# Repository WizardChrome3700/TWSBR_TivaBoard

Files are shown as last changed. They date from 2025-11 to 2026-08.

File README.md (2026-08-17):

### Project Report:-
[Group I ME6102 Presentation .pdf](https://github.com/WizardChrome3700/TWSBR_TivaBoard/blob/master/Group%20I%20ME6102%20Presentation%20.pdf) is the project presentation. There was no report but we were required to submit [build instructions](https://github.com/WizardChrome3700/TWSBR_TivaBoard/blob/master/Build_instructions.pdf).

### Pinout of Tiva C Launchpad
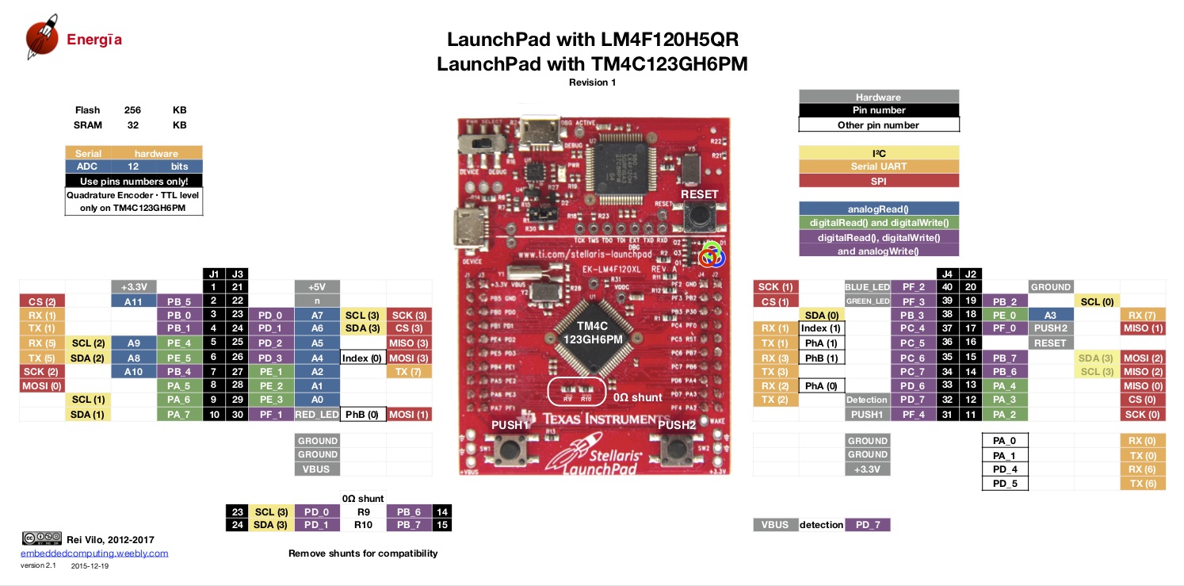
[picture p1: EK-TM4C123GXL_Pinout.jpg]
TIVA TM4C123GH6PM


### Connection Summary
|Component|Pin|Connected To |Signal |Description |
|---|---|---|---|---|
|JST6A |1  |TB1 pin 1 |motor1_M1 |Motor 1 terminal A |
|JST6A |2  |Tiva +3.3 V |3V3 |Encoder supply |
|JST6A |3  |Tiva PC5 |Encoder1_PHA |Encoder Channel A |
|JST6A |4  |Tiva PC6 |Encoder1_PHB |Encoder Channel B |
|JST6A |5  |Tiva GND |GND |Common ground |
|JST6A |6  |TB1 pin 2 |motor1_M2 |Motor 1 terminal B |
|JST3A |1  |Tiva PB4 |IN1_motor_driver |Motor 1 input 1 |
|JST3A |2  |Tiva PB5 |IN2_motor_driver |Motor 1 input 2 |
|JST3A |3  |Tiva PE4 |ENA_motor_driver |Motor 1 enable signal |
|JST6B |1  |TB2 pin 1 |motor2_M2 |Motor 2 terminal A |
|JST6B |2  |Tiva +3.3 V |3V3 |Encoder supply |
|JST6B |3  |Tiva PF0 |Encoder2_PHA |Encoder Channel A |
|JST6B |4  |Tiva PD7 |Encoder2_PHB |Encoder Channel B |
|JST6B |5  |Tiva GND |GND |Common ground |
|JST6B |6  |TB2 pin 2 |motor2_M1 |Motor 2 terminal B |
|JST3B |1  |Tiva PB6 |IN3_motor_driver |Motor 2 input 1 |
|JST3B |2  |Tiva PB7 |IN4_motor_driver |Motor 2 input 2 |
|JST3B |3  |Tiva PD6 |ENB_motor_driver |Motor 2 enable signal |
|TB1 |1  |JST6A pin 1 |motor1_M1 |Motor 1 terminal A |
|TB1 |2  |JST6A pin 6 |motor1_M2 |Motor 1 terminal B |
|TB2 |1  |JST6B pin 1 |motor2_M2 |Motor 2 terminal A |
|TB2 |2  |JST6B pin 6 |motor2_M1 |Motor 2 terminal B |
|R1 |-  |3.3V ↔ Tiva PB2|4.7kΩ |Pull-up or signal conditioning |
|R2 |-  |3.3V ↔ Tiva PB3|4.7kΩ |Pull-up or signal conditioning |
|ESP01 |7  |Tiva PB1 |ESP_RX |UART Recieve(ESP) to UART Transmit(Tiva)|
|ESP01 |2  |Tiva PB0 |ESP_TX |UART Transmit(ESP) to UART Recieve(Tiva)|
|ESP01 |8  |Tiva +3.3 V |3V3 |Power ESP01 |
|ESP01 |1  |Tiva GND |GND |Common ground |
|ESP01 |4  |Tiva +3.3 V |ESP_CH_EN |Enable ESP01 to communicate |
|MPU9250  |1  |Tiva +3.3 V |MPU9520_VCC |Power MPU9250 |
|MPU9250  |2  |Tiva GND |GND |Common ground |
|MPU9250  |3  |Tiva PB2 |MPU9520_SCL |Serial clock of I2C of MPU9250 |
|MPU9250  |4  |Tiva PB3 |MPU9520_SDA |Serial data of I2C of MPU9250 |
|RLS08 |A1 |Tiva PD0 |Line follower IR1|ADC source of IR1 of Line follower |
|RLS08 |A2 |Tiva PD1 |Line follower IR1|ADC source of IR1 of Line follower |
|RLS08 |A3 |Tiva PD2 |Line follower IR1|ADC source of IR1 of Line follower |
|RLS08 |A4 |Tiva PD3 |Line follower IR1|ADC source of IR1 of Line follower |
|RLS08 |A5 |Tiva PE1 |Line follower IR1|ADC source of IR1 of Line follower |
|RLS08 |A6 |Tiva PE2 |Line follower IR1|ADC source of IR1 of Line follower |
|RLS08 |A7 |Tiva PE3 |Line follower IR1|ADC source of IR1 of Line follower |
|RLS08 |A8 |Tiva PE0 |Line follower IR1|ADC source of IR1 of Line follower |

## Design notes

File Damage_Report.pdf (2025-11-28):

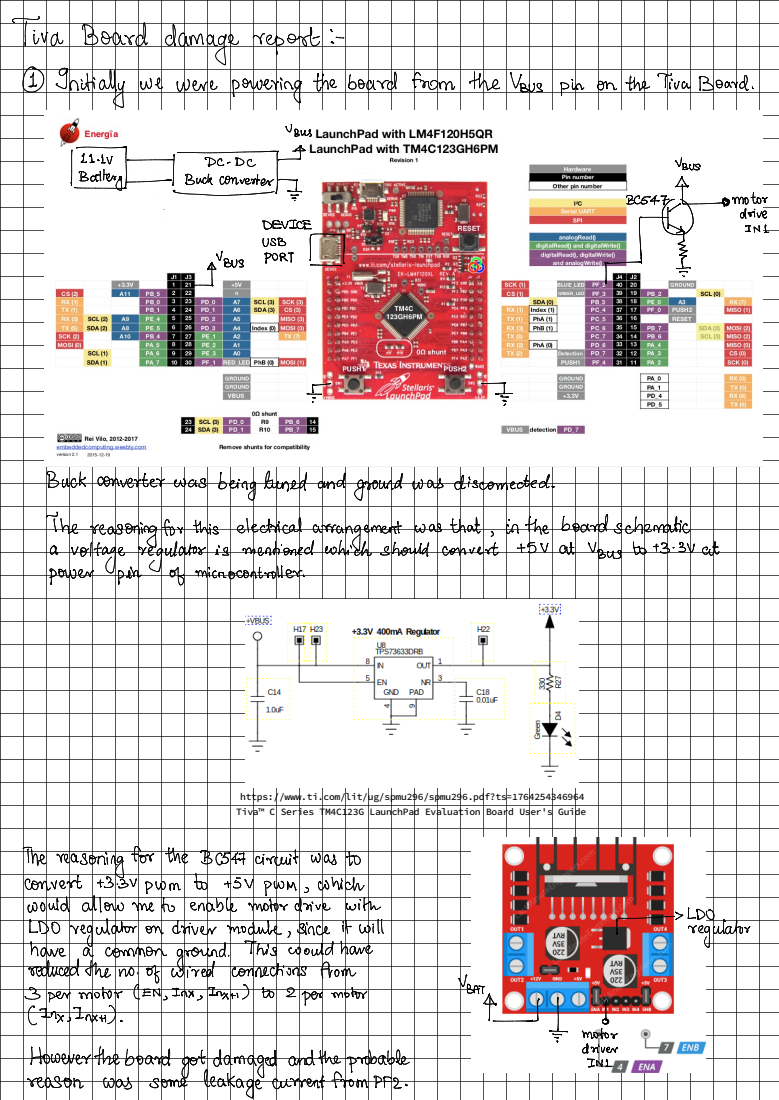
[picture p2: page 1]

https://www.ti.com/lit/ug/spmu296/spmu296.pdf?ts=1764254346964
Tiva™ C Series TM4C123G LaunchPad Evaluation Board User's Guide

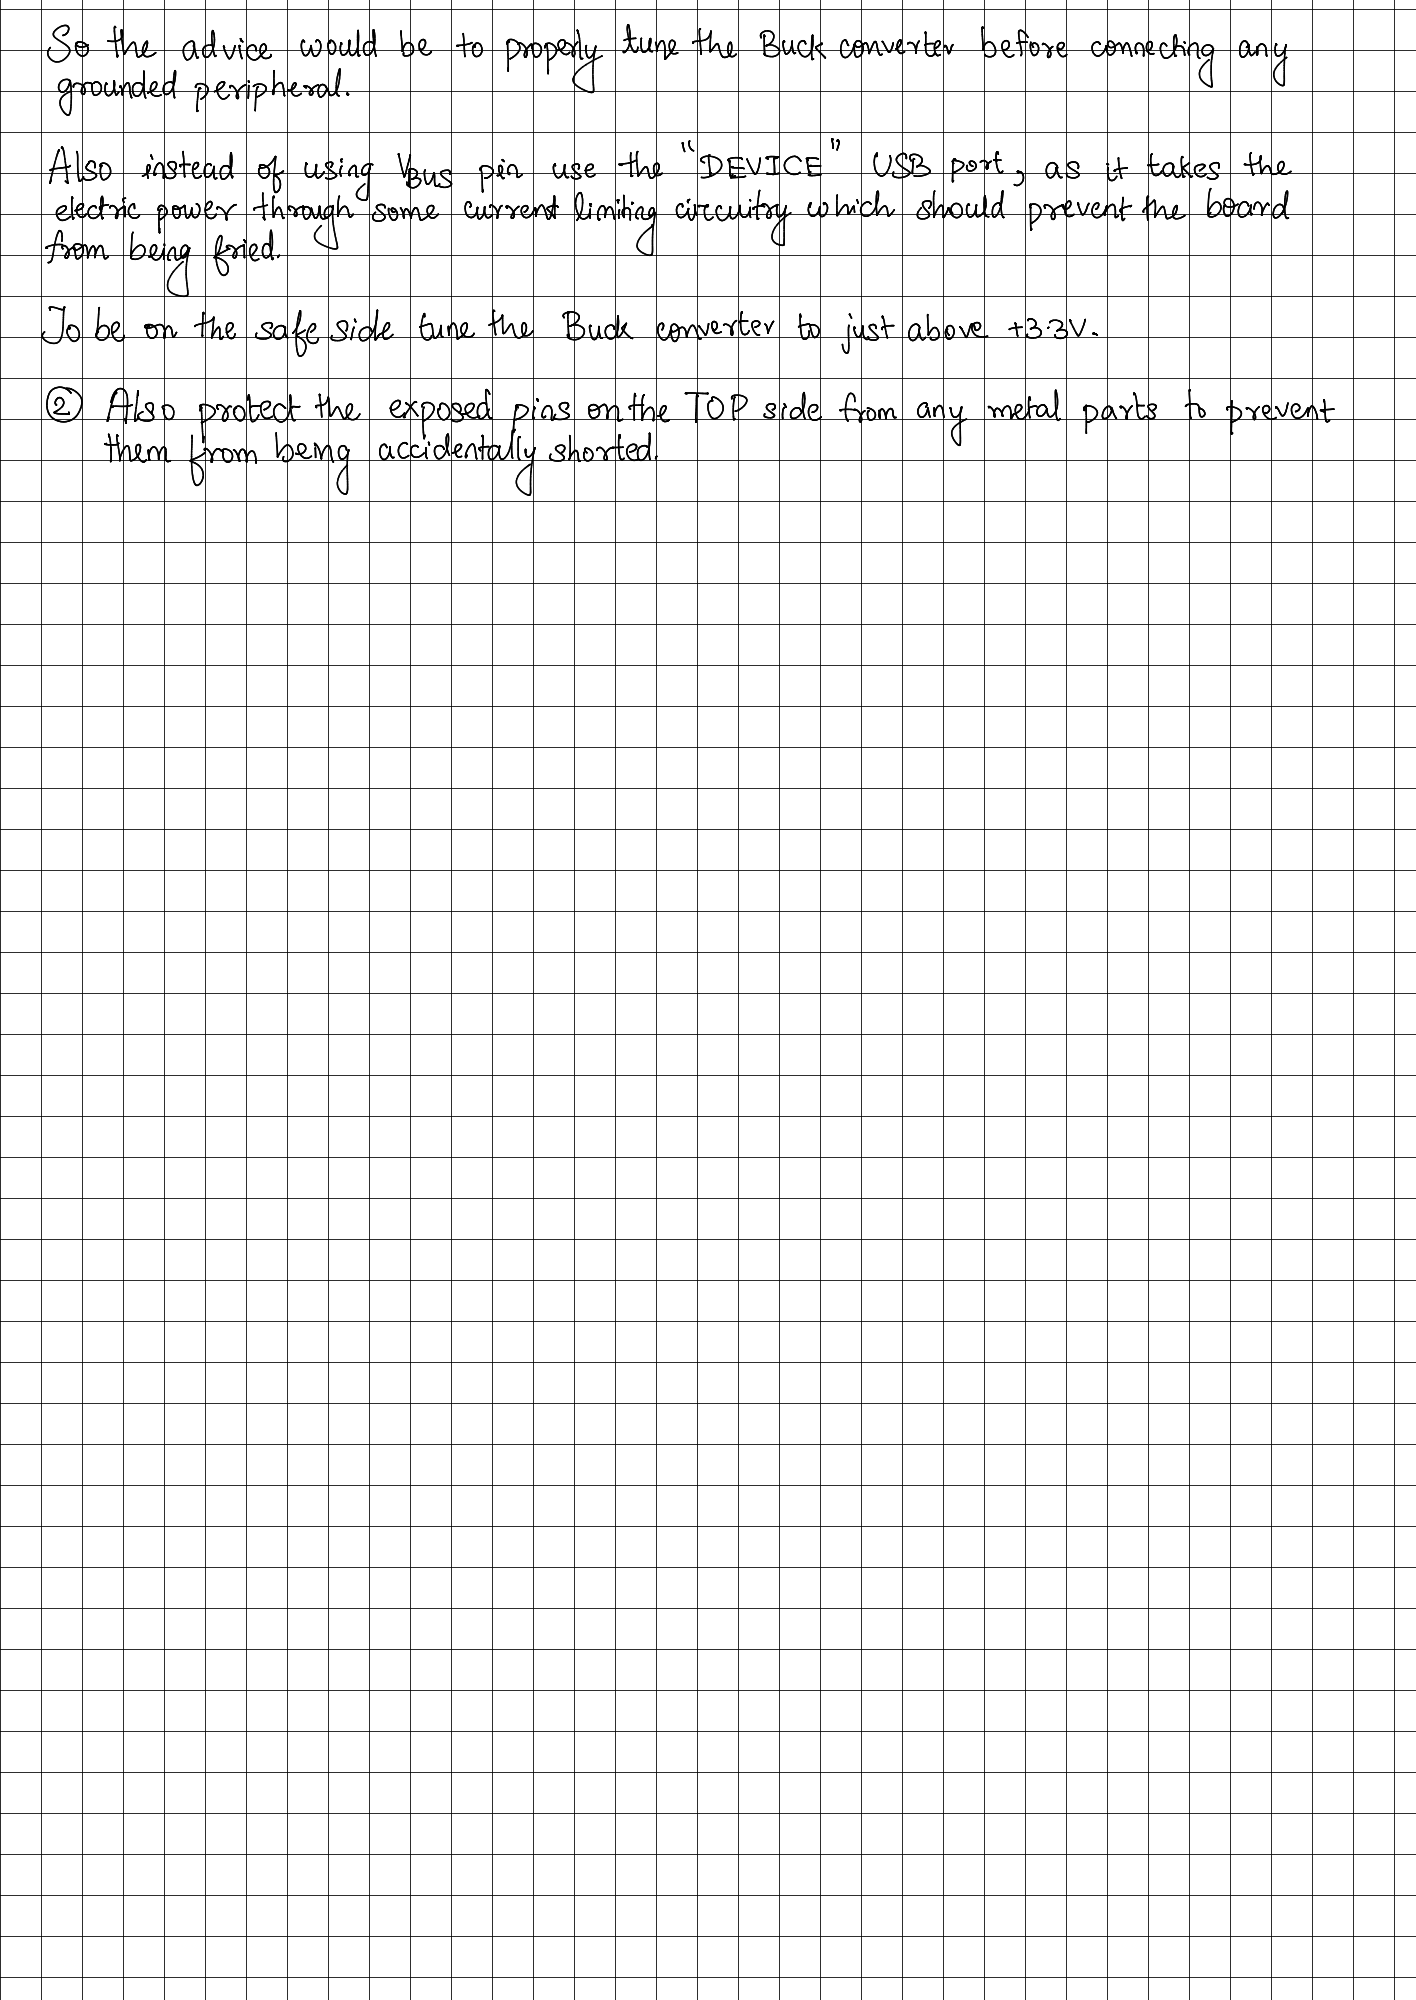
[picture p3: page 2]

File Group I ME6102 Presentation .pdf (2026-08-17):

# Design and Development of Self-Balancing Mobile Robot

Presented by- Group 1

Under the Guidance of

## (Prof. Prasanna S Gandhi)

# ME 6102- Project Stage IV

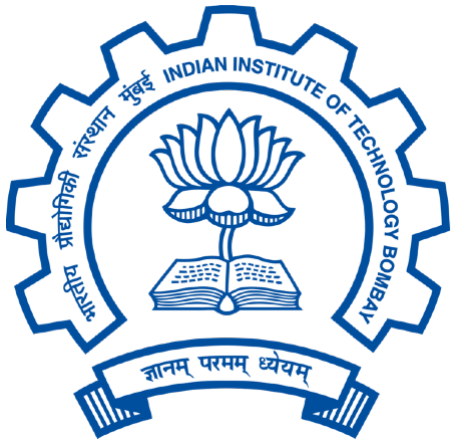
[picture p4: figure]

Indian Institute of Technology, Bombay

November 2025

## Department of Mechanical Engineering

Akshat Panda | Nishad PS | Sajal Thomas

# OUTLINE

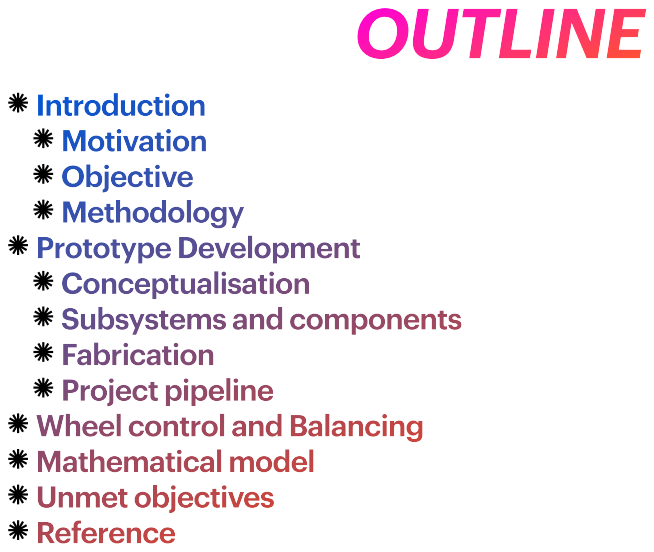
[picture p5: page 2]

Introduction
Motivation
Objective
Methodology
Prototype Development
Conceptualisation
Subsystems and components
Fabrication
Project pipeline
Wheel control and Balancing
Mathematical model
Unmet objectives
Reference

# Motivation

# Objective

# Methodology

We used the Tiva C Series microcontroller as the main controller for all real-time operations.
The robot integrates IMU for tilt estimation and encoders for wheel speed feedback. The mechanical structure is made using laser-cut acrylic plates assembled with spacers. The electrical system (motor driver, buck converter, sensors) is neatly integrated with the chassis.
The firmware was developed in Code Composer Studio using TivaWare driver libraries.

Design and development of a robot with TIVA microcontroller capable of self balancing and line following capabilities

To study the real world application of inverted single pendulum system Demonstrates practical implementation of PID control, sensor fusion, and real-time embedded processing.

# System Layout

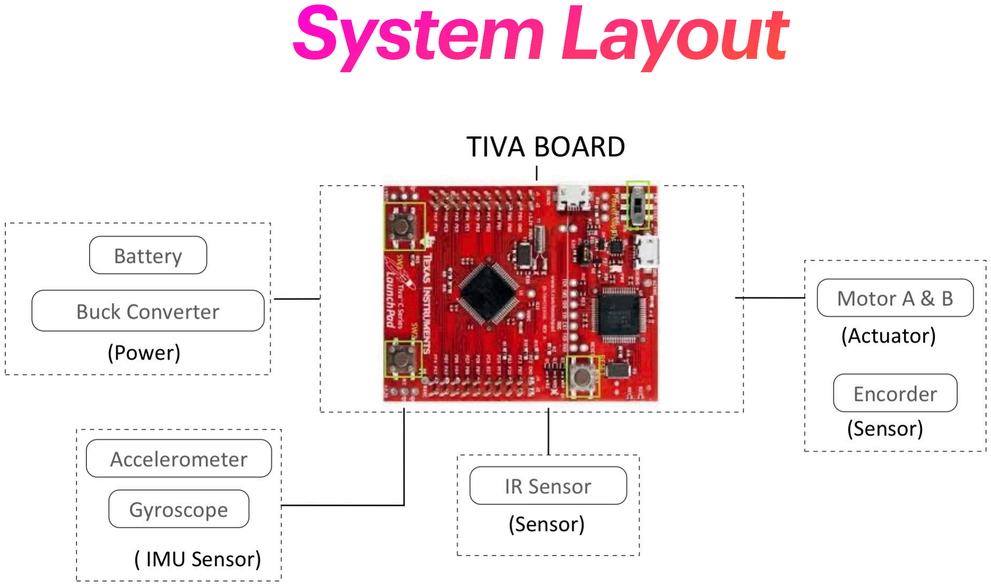
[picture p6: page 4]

# Conceptualisation

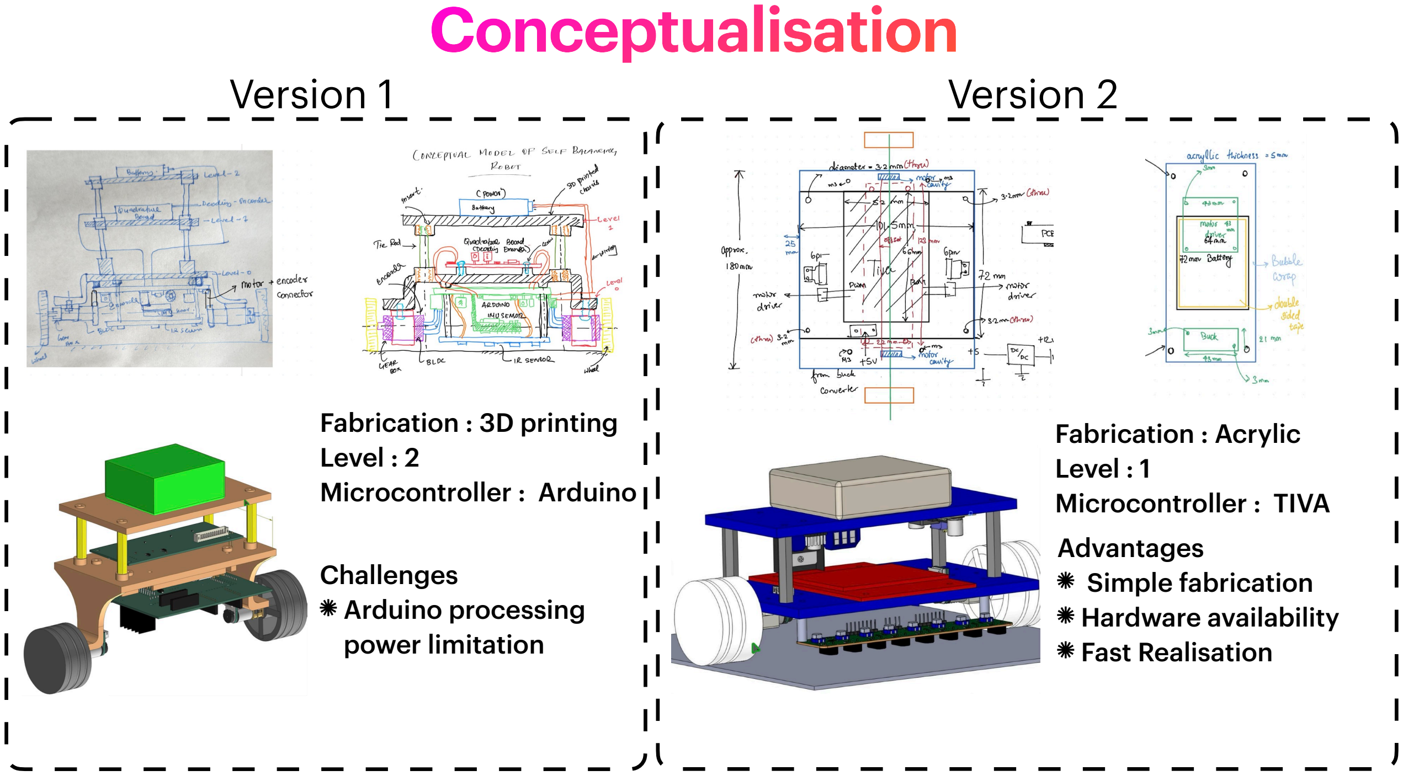
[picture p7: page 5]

Version 1 | Version 2

Fabrication : 3D printing
Level : 2
Microcontroller : Arduino

Challenges
Arduino processing
power limitation

Fabrication : Acrylic
Level : 1
Microcontroller : TIVA
Advantages
Simple fabrication
Hardware availability
Fast Realisation

# Specifications

### Microcontroller : TIVA C series Motor : GA12- N20 DC Motor (12V) Buck Converter - LM2596S Motor Drive - L298N Wheel - N20 Wheel 44mm dia Sensors - Encorder : Pro-range OE-28 - IMU - MPU 9250 - IR - RLS 08 Analog & Digital Line sensor array

# System Layout

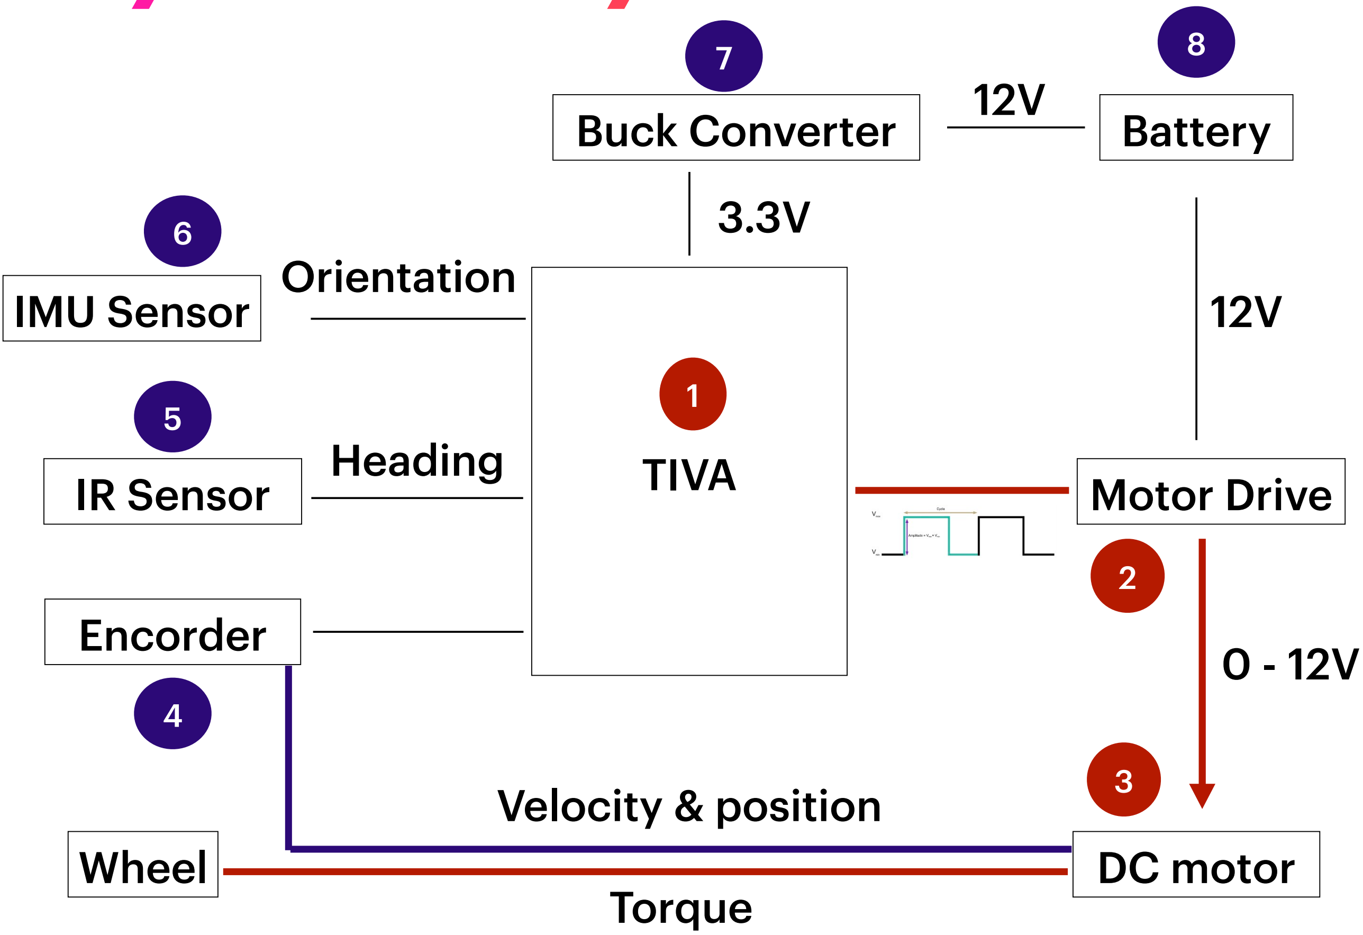
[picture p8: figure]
Wheel; DC motor; Motor Drive; Buck Converter; Battery; TIVA IR Sensor; IMU Sensor; Encorder; Velocity & position; Heading; Orientation; Torque
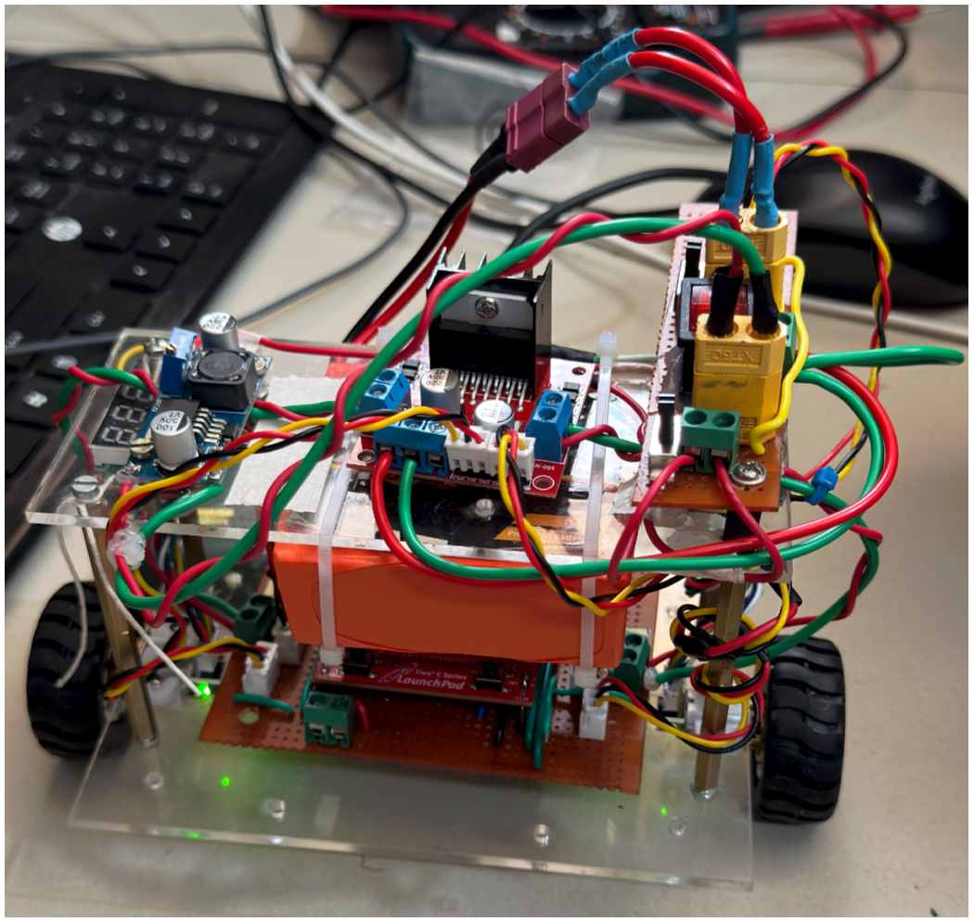
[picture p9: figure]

# Fabrications

## Mechanical integration

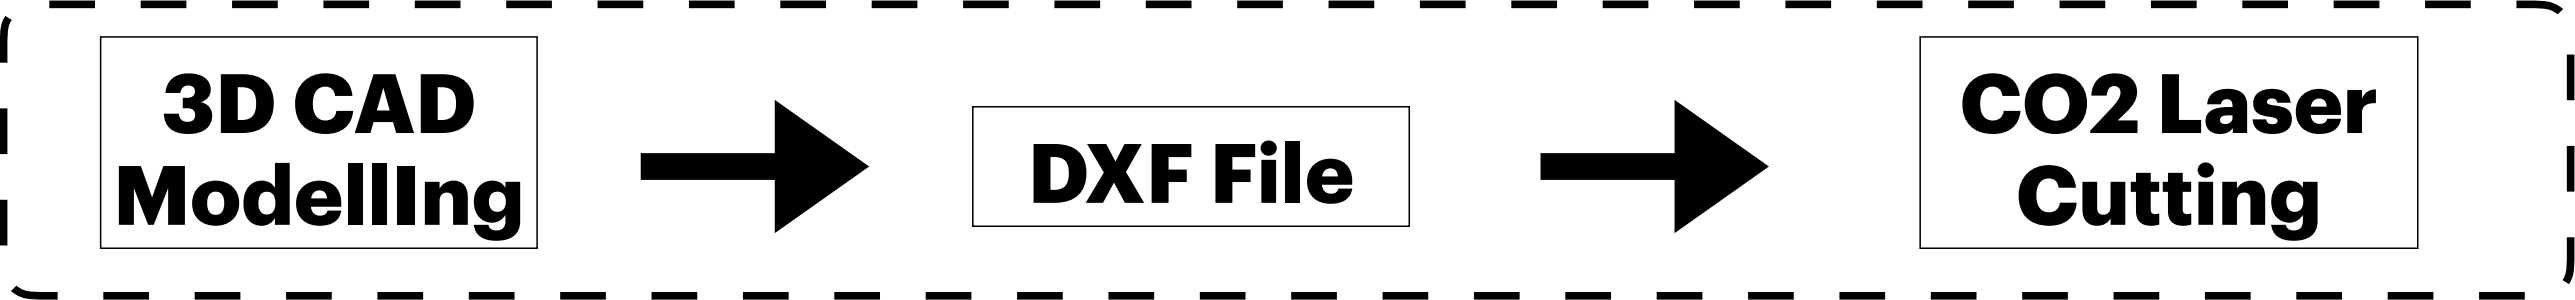
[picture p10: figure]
3D CAD; ModellIng; DXF File; CO2 Laser Cutting

## Electrical integration

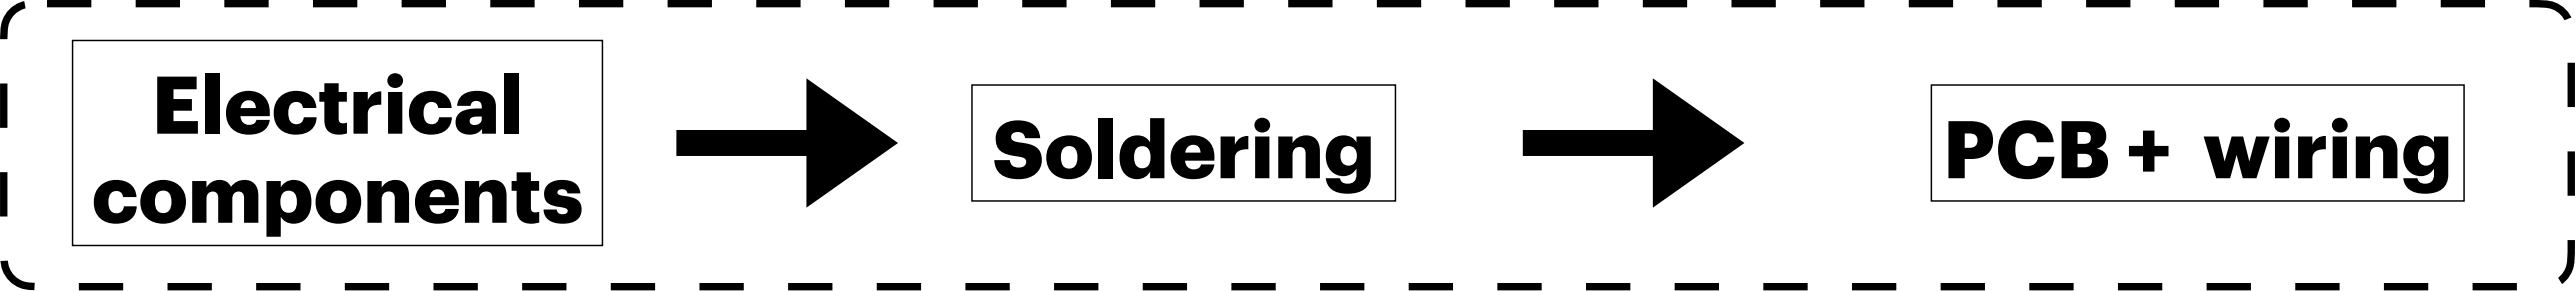
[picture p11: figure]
Electrical; components; Soldering; PCB + wiring
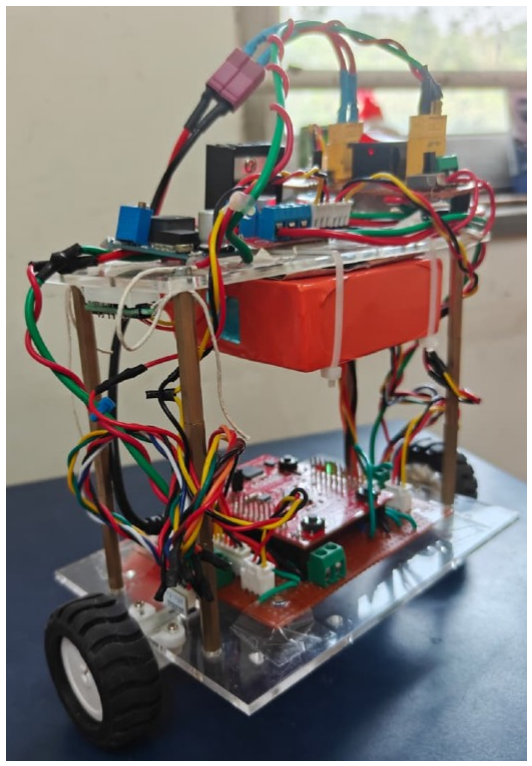
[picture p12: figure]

Laser cut acrylic

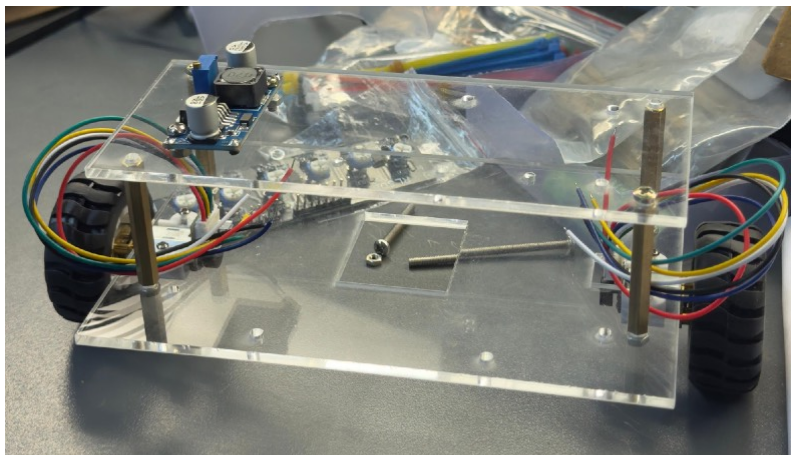
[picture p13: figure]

sheet | Assembly of both the
| levels

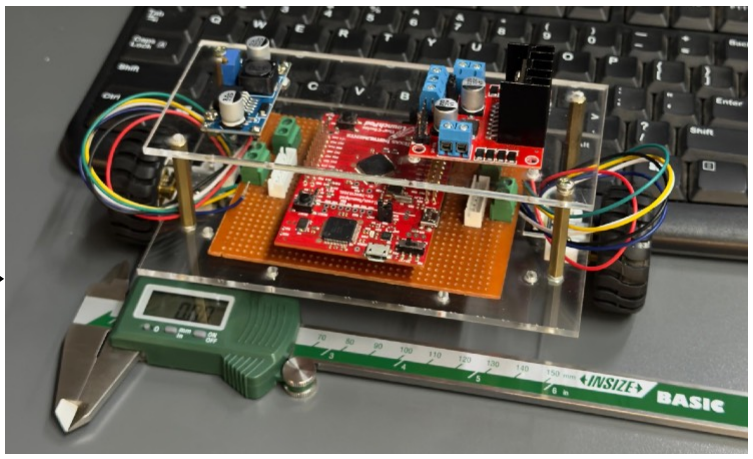
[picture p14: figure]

Assembly of TiVA
Microcontroller 3D CAD

# PROJECT PIPELINE

23 SEP | 23OCT | 05 Nov | 23 Nov

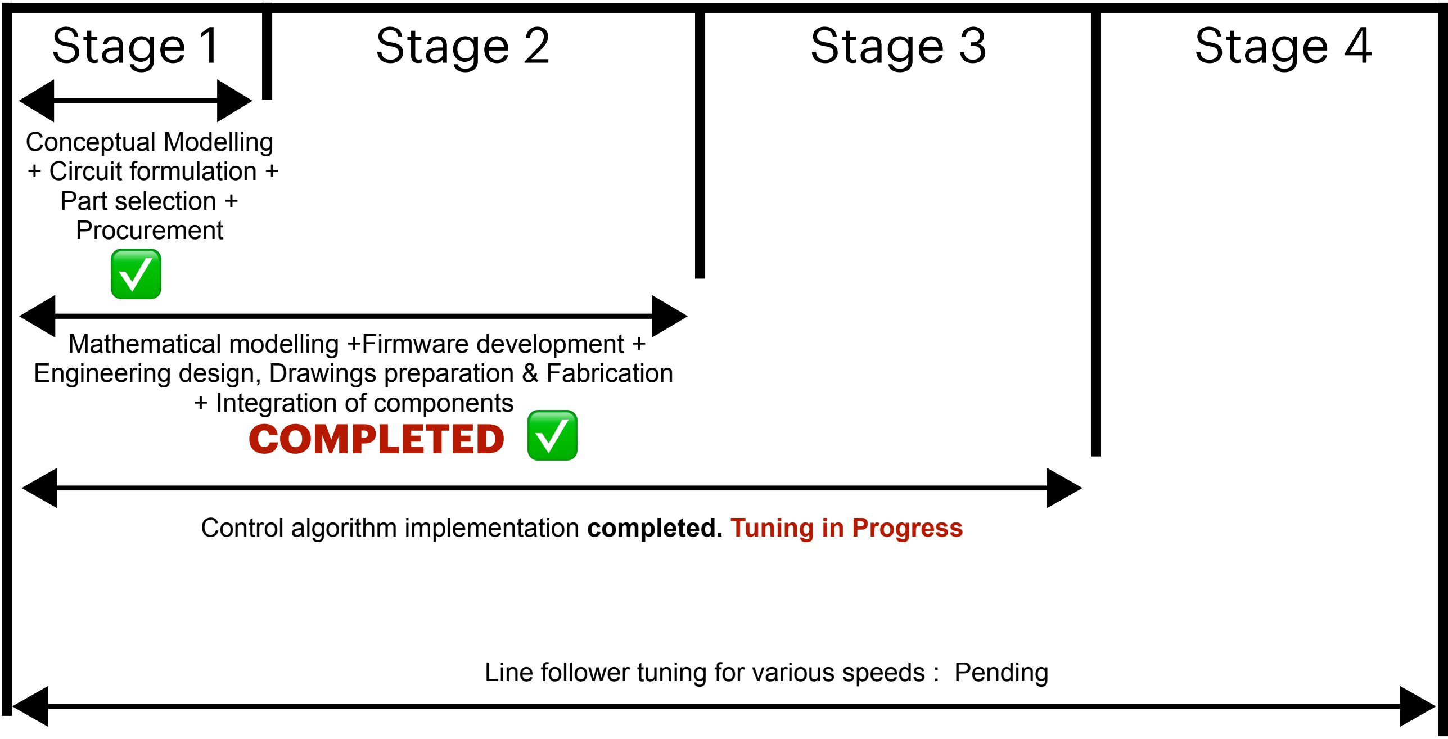
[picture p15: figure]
Stage 1; Stage 2; Stage 3; Stage 4; Conceptual Modelling + Circuit formulation + Part selection + Procurement; Mathematical modelling +Firmware development +; + Integration of components; COMPLETED

Engineering design, Drawings preparation & Fabrication

Control algorithm implementation completed. Tuning in Progress

Line follower tuning for various speeds : Pending

# Wheel Control

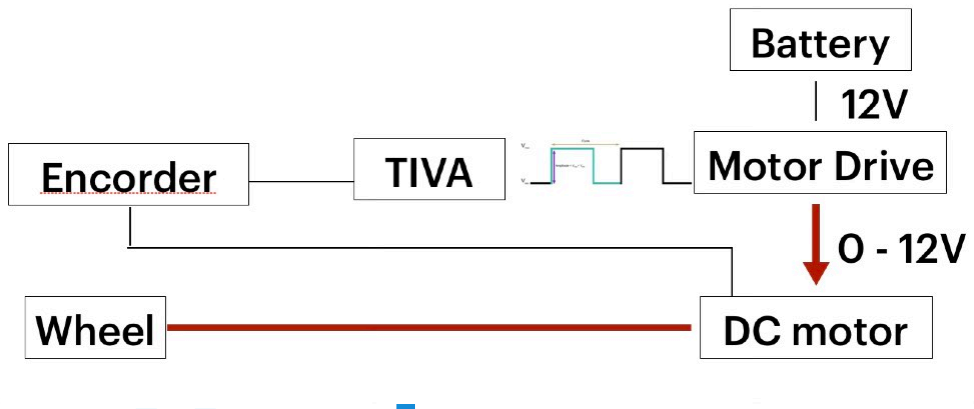
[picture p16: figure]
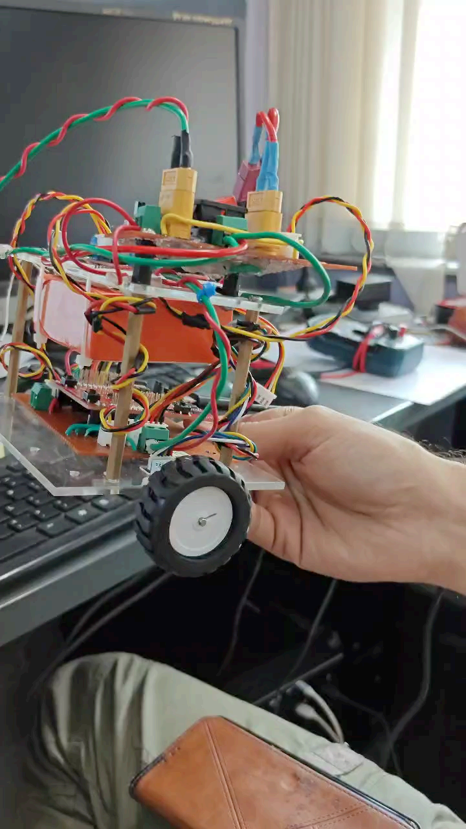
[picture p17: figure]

Micro Controller
TIVA C- Series
Battery
12V - Lithium ion battery
2500 mAH
Motor drive
L 298N
Voltage O/P: 0 - 12 V
Gear Ratio - 250:1
Motor
N20 DC motor

### 12 V, 0.6A

Torque = 2N-cm
Encorder
3 Pulse Per Revelution.

## Hardware

## Software

Software : Code Composer
Studio
Objective : Intuitive wheel control
Current Status : PWM
generation and Encorder
reading completed

Wheel control code (https://github.com/WizardChrome3700/TWSBR_TivaBoard/tree/master/TWSBR_Code_Base/TWSBR_Wheel)

# BALANCE CONTROL

## Hardware

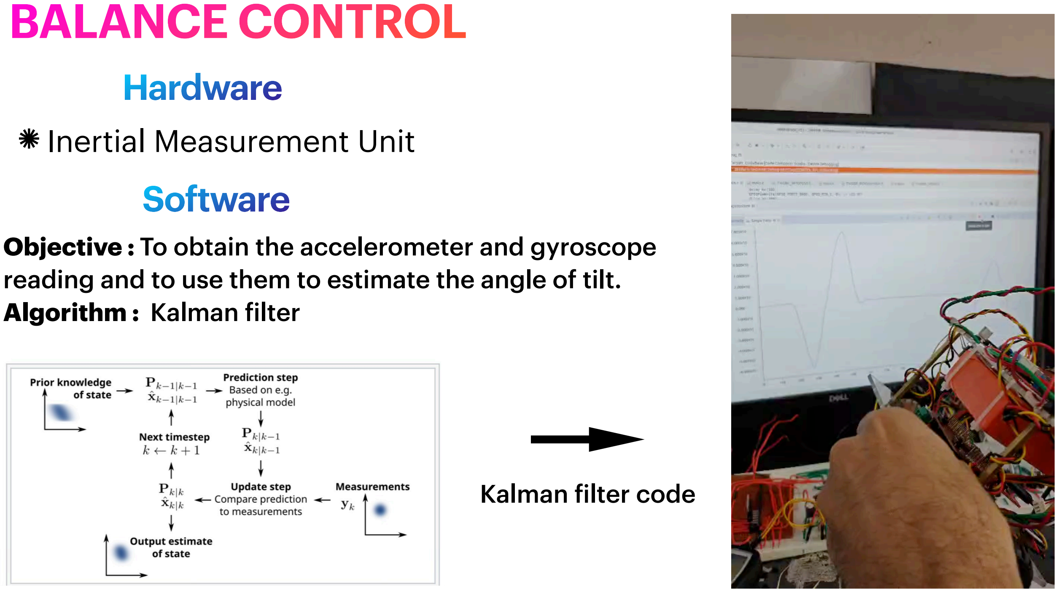
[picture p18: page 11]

### Inertial Measurement Unit

## Software

Objective : To obtain the accelerometer and gyroscope reading and to use them to estimate the angle of tilt. Algorithm : Kalman filter

Kalman filter code (https://github.com/WizardChrome3700/TWSBR_TivaBoard/tree/master/TWSBR_Code_Base/TWSBR_MPU9250)

# Mathematical modelling - Dynamics

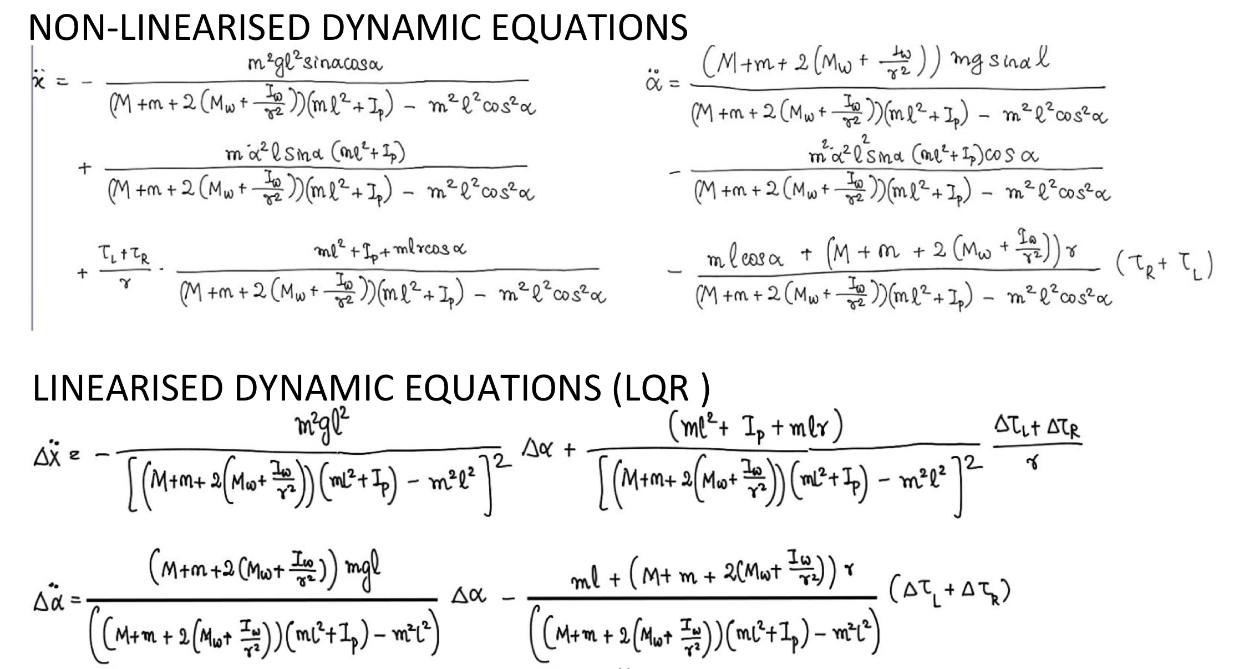
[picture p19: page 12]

# Mathematical modelling - Kalman Filter

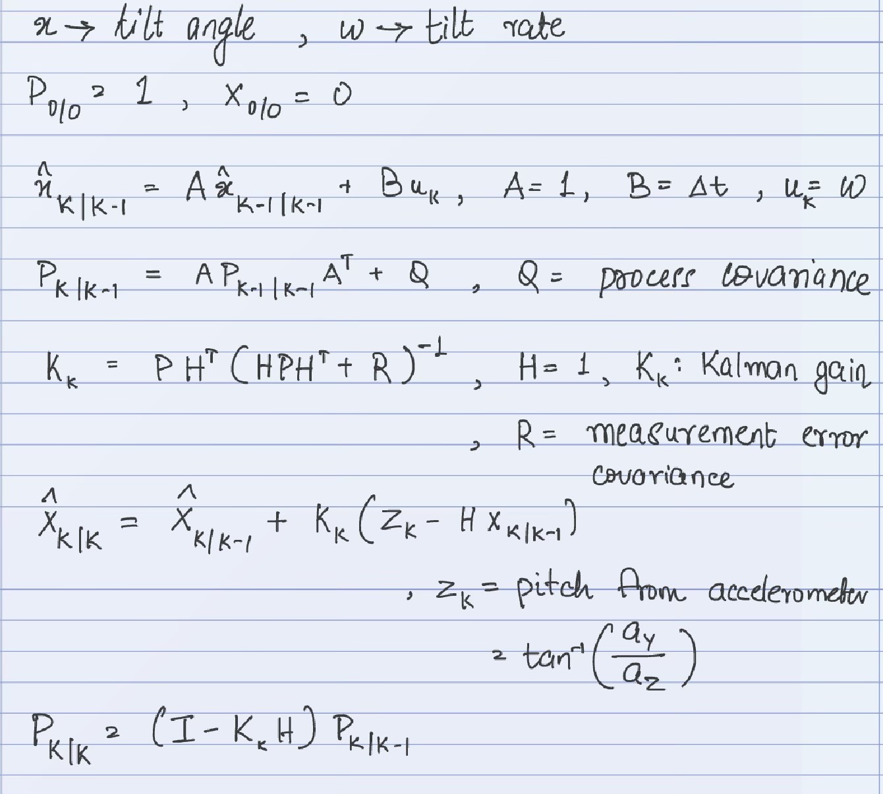
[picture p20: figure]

# Input and output of kalman filter

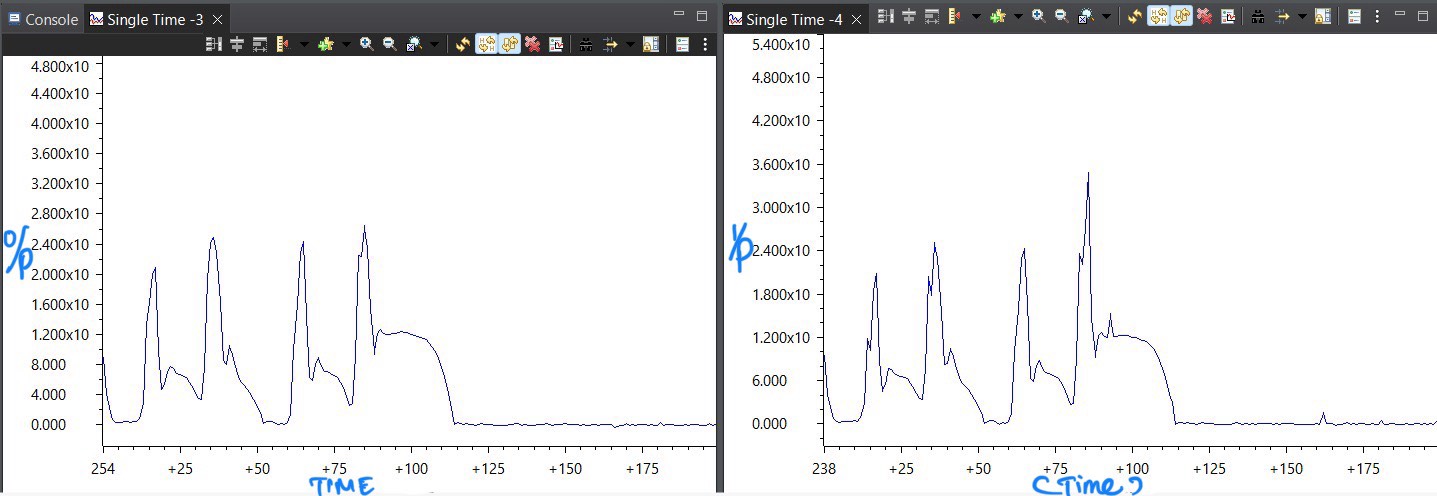
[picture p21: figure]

# UNMET OBJECTIVES

## Line-Following Feature Not Integrated Complete Stability Not Achieved

Despite integrating the IMU, motor driver, and Tiva C controller successfully, the robot did not reach complete stability because the PID control parameters (Kp, Ki, Kd) could not be fully optimized.
We performed multiple experiments by varying these gains, but the system continued to show oscillations and drift.
Achieving stable balance requires extensive tuning under different loading and surface conditions, which we could not complete within the available time. Therefore, additional testing and further PID refinement are needed to meet the stability objective

# Reason for not meeting the objectives

# Reference

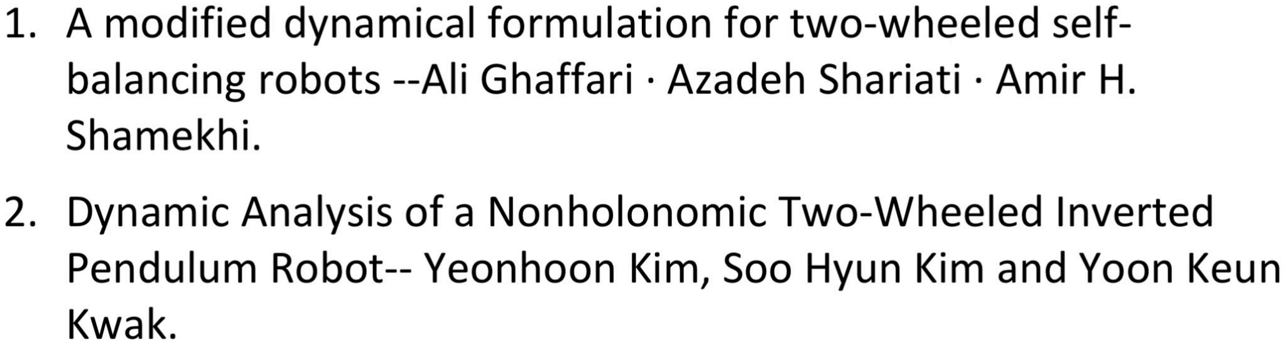
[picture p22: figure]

# Thank you

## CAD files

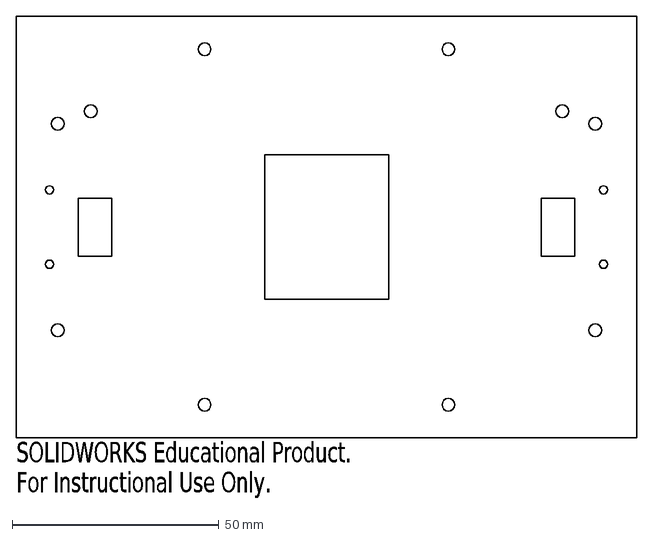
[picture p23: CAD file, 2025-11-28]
Mechanical Subsystem/Level0.DXF
SOLIDWORKS Educational Product.
For Instructional Use Only.

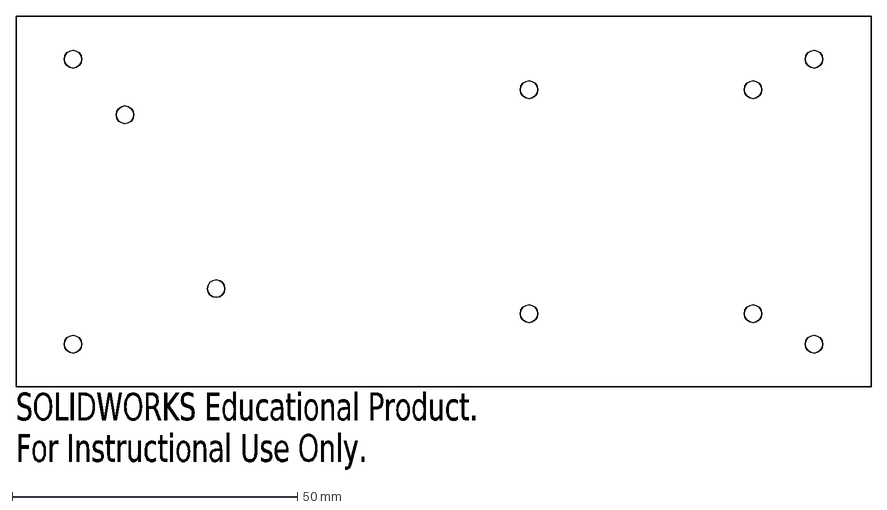
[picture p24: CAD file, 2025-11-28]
Mechanical Subsystem/Level1.DXF
SOLIDWORKS Educational Product.
For Instructional Use Only.

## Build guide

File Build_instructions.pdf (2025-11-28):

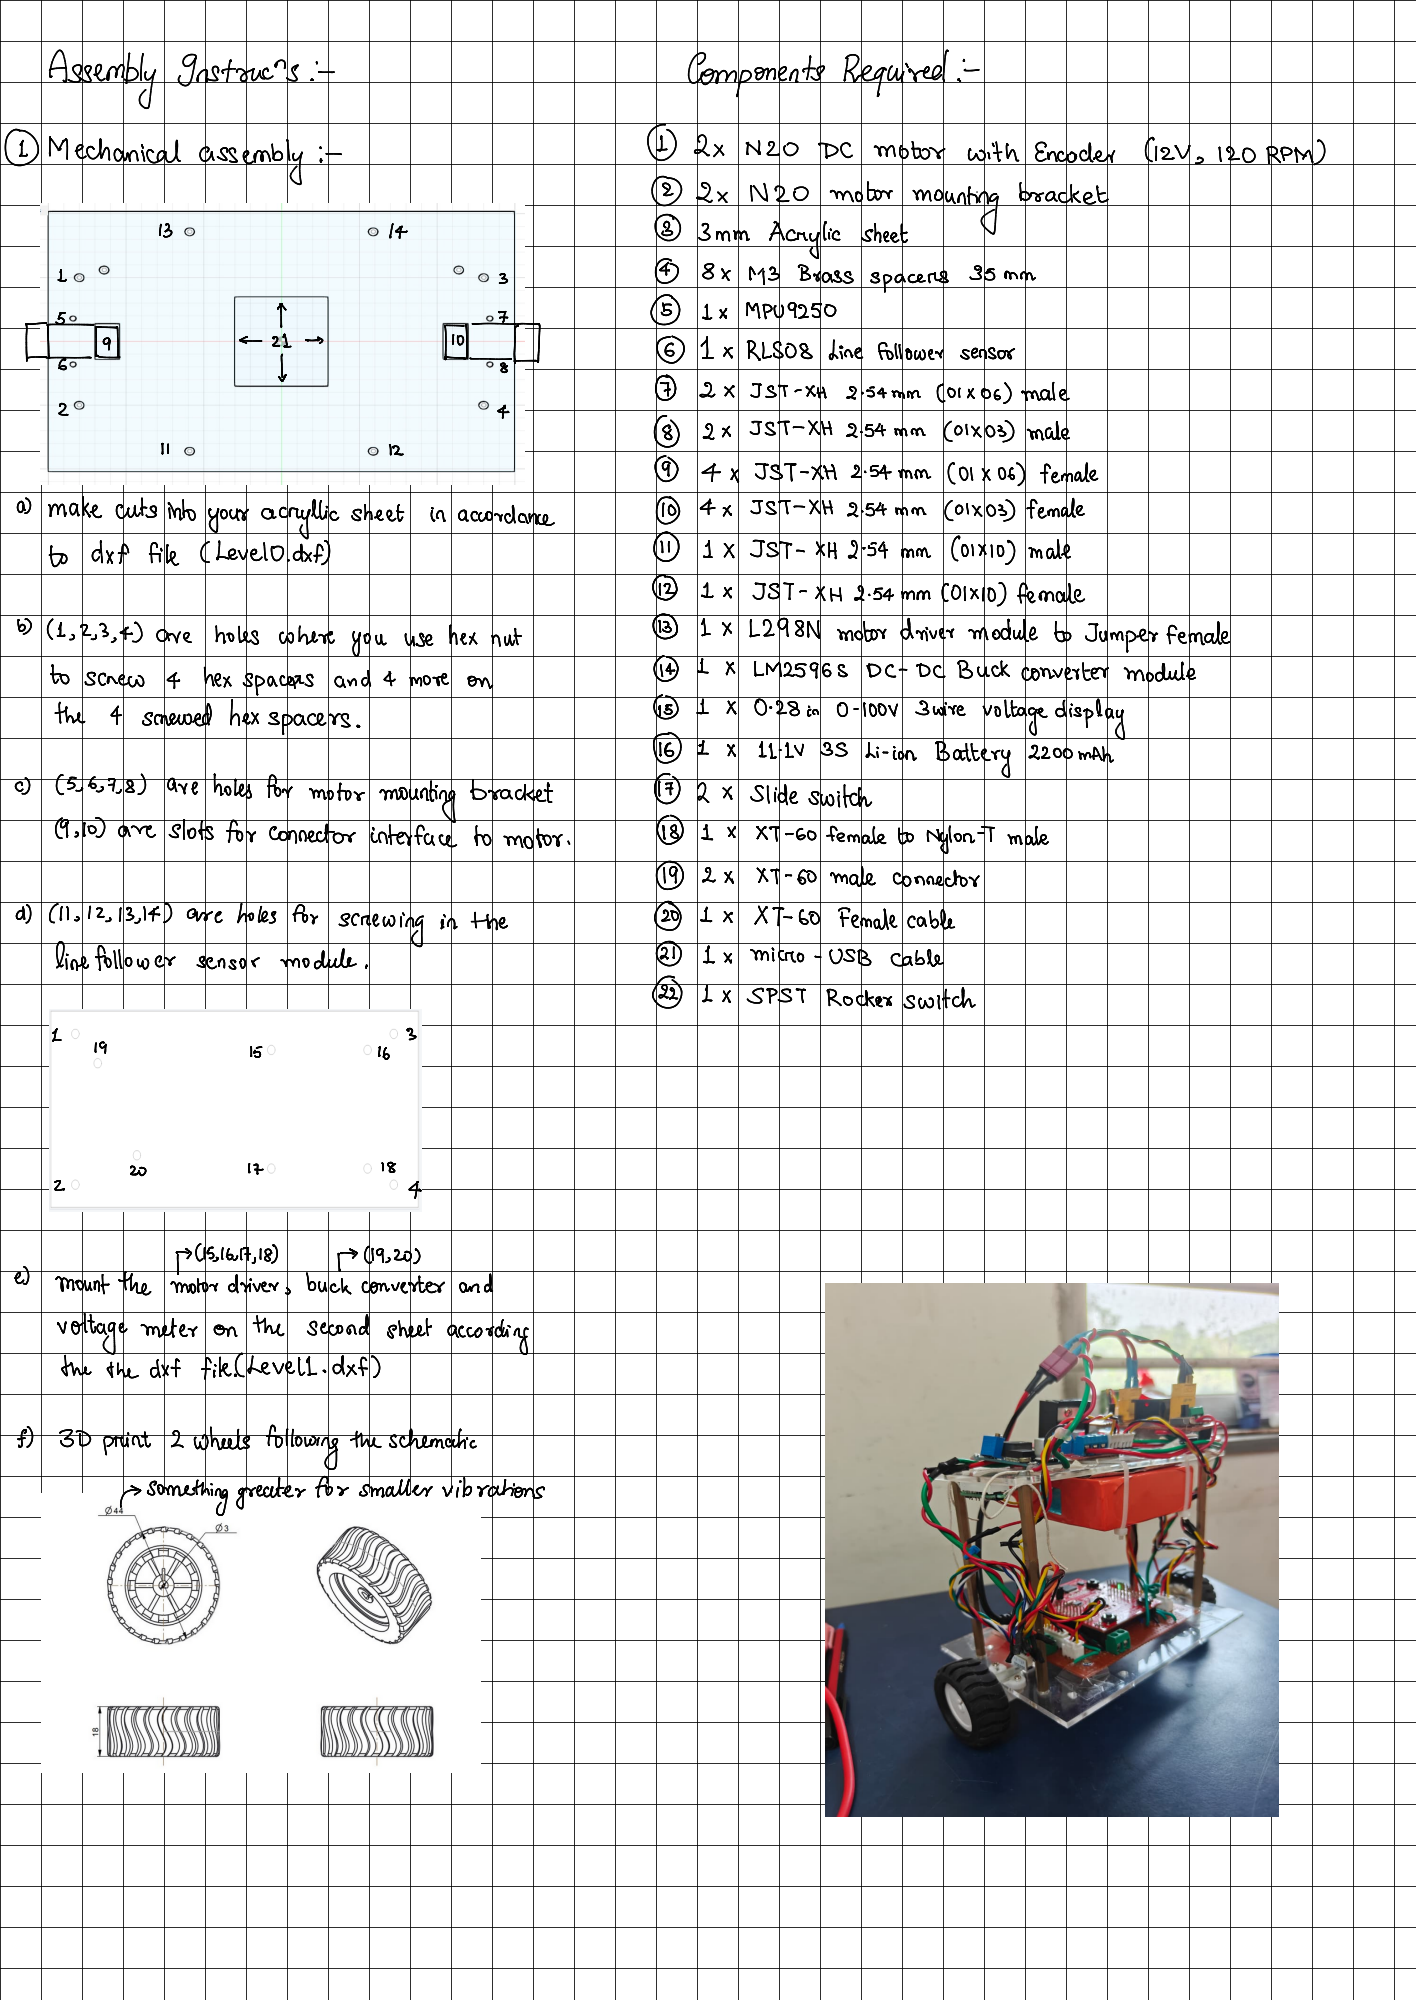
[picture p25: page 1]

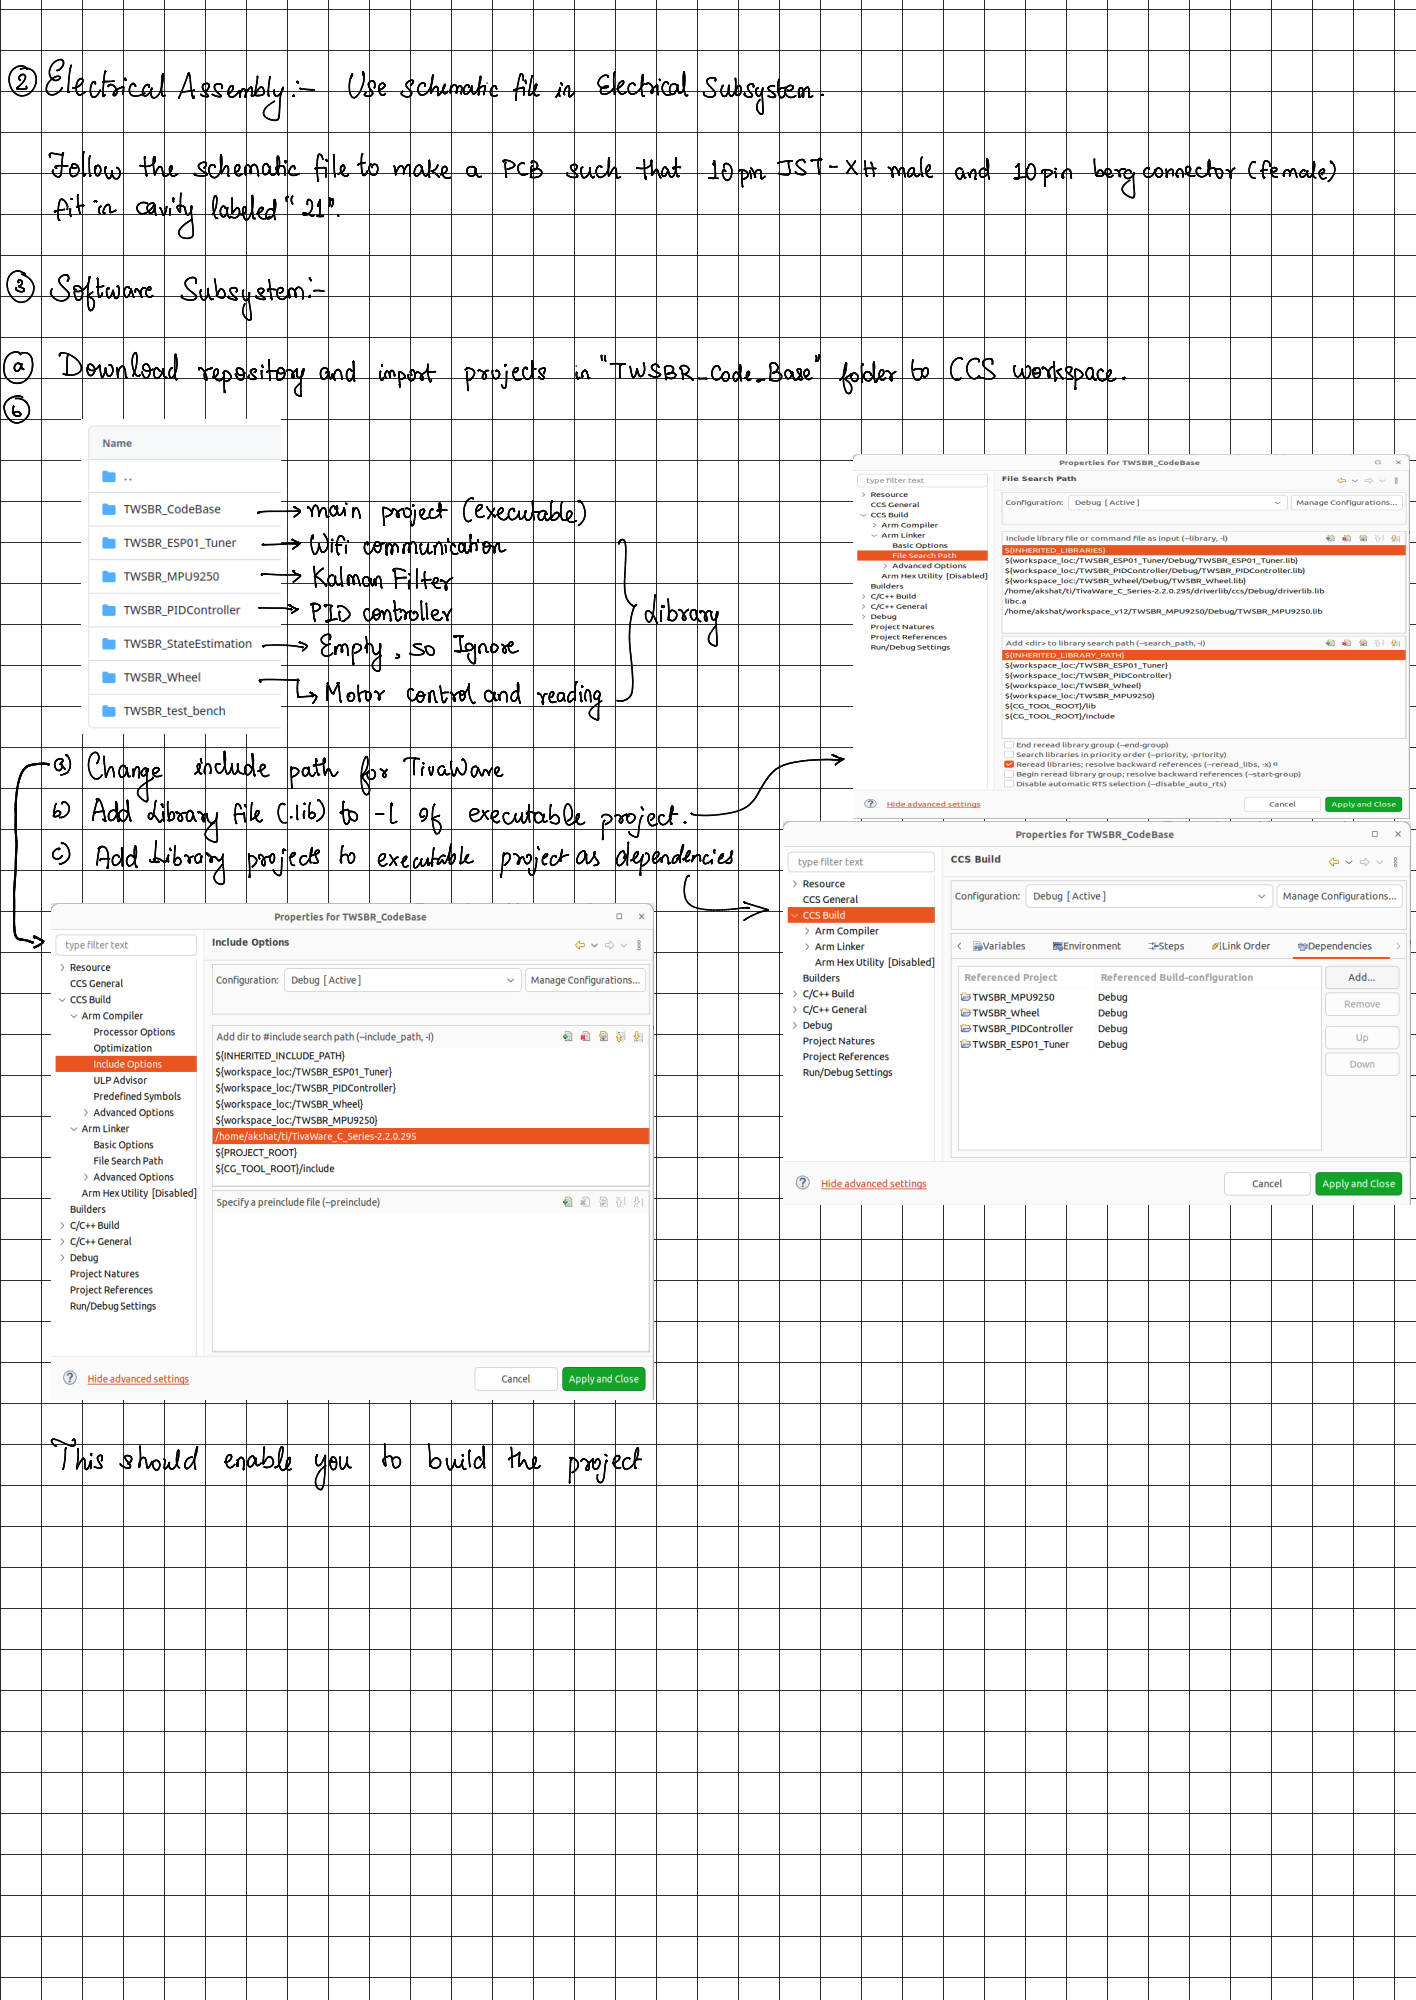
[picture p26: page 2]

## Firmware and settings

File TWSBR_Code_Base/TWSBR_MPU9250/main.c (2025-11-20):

#include <stdbool.h>
#include <stdint.h>
#include <stdlib.h>
#include <math.h>
#include <string.h>

#include "inc/hw_memmap.h"
#include "inc/hw_types.h"
#include "inc/hw_gpio.h"
#include "inc/hw_uart.h"
#include "driverlib/gpio.h"
#include "driverlib/sysctl.h"
#include "driverlib/pin_map.h"
#include "driverlib/i2c.h"
#include "driverlib/uart.h"
#include "driverlib/rom.h"
#include "driverlib/rom_map.h"

#include "TWSBR_MPU9250.h"

// I2C & MPU constants
#define ACCEL_ADDR 0x3B
#define GYRO_ADDR  0x43
#define devAddr    0x68

#define I2C_TIMEOUT_ATTEMPTS 3
#define I2C_BUSY_TIMEOUT 4000

// Filtering & Kalman parameters (tune as needed)
#define ACCEL_LPF_TAU        0.02f   // seconds
#define ACCEL_MEDIAN_SAMPLES 3
#define KAL_Q_ANGLE          0.001f
#define KAL_Q_BIAS           0.003f
#define KAL_R_MEAS           0.03f
#define ACCEL_MAG_THRESHOLD  0.25f   // g units

// PID parameters (tune to your motors & robot)
#define PID_KP  30.0f
#define PID_KI  0.5f
#define PID_KD  1.0f
#define PID_I_CLAMP  100.0f
#define PID_DEADZONE_DEG 0.7f   // degrees

// ---------- simple helpers ----------
static float median3(float a, float b, float c)
{
    if ((a <= b && b <= c) || (c <= b && b <= a)) return b;
    if ((b <= a && a <= c) || (c <= a && a <= b)) return a;
    return c;
}

static float lpf_update(float prev, float in, float dt, float tau)
{
    if (tau <= 0.0f) return in;
    float alpha = dt / (tau + dt);
    return prev + alpha * (in - prev);
}

// simple blocking delays using SysCtlDelay
void delay_ms(uint16_t delay)
{
    // SysCtlDelay counts 3 cycles per loop
    uint32_t loops = (SysCtlClockGet() / 3000) * delay;
    SysCtlDelay(loops);
}
void delay_us(uint16_t delay)
{
    uint32_t clockFreq = SysCtlClockGet();
    uint32_t loops = (uint32_t)(((uint64_t)clockFreq * delay) / 3000000);
    SysCtlDelay(loops);
}

// ---------- I2C bus recovery / checks (PB2: SCL, PB3: SDA) ----------
void recover_i2c_bus(void)
{
    // Make pins GPIO outputs to toggle SCL until SDA releases
    GPIOPinTypeGPIOOutput(GPIO_PORTB_BASE, GPIO_PIN_2 | GPIO_PIN_3);

    // Drive both high first
    GPIOPinWrite(GPIO_PORTB_BASE, GPIO_PIN_2 | GPIO_PIN_3, GPIO_PIN_2 | GPIO_PIN_3);
    delay_ms(1);

    int i = 0;
    while(i < 16) {
        // clock low
        GPIOPinWrite(GPIO_PORTB_BASE, GPIO_PIN_2, 0);
        delay_us(5);

        // check SDA
        if(GPIOPinRead(GPIO_PORTB_BASE, GPIO_PIN_3) & GPIO_PIN_3) {
            // SDA released; pulse one more time and break
            GPIOPinWrite(GPIO_PORTB_BASE, GPIO_PIN_2, GPIO_PIN_2);
            delay_us(5);
            break;
        }

        // drive clock high
        GPIOPinWrite(GPIO_PORTB_BASE, GPIO_PIN_2, GPIO_PIN_2);
        delay_us(5);
        i++;
    }

    // send STOP: SDA low -> high while SCL high
    GPIOPinWrite(GPIO_PORTB_BASE, GPIO_PIN_3, 0);
    delay_us(5);
    GPIOPinWrite(GPIO_PORTB_BASE, GPIO_PIN_2, GPIO_PIN_2);
    delay_us(5);
    GPIOPinWrite(GPIO_PORTB_BASE, GPIO_PIN_3, GPIO_PIN_3);
    delay_us(5);

    // restore I2C pin functions
    GPIOPinConfigure(GPIO_PB2_I2C0SCL);
    GPIOPinConfigure(GPIO_PB3_I2C0SDA);
    GPIOPinTypeI2CSCL(GPIO_PORTB_BASE, GPIO_PIN_2);
    GPIOPinTypeI2C(GPIO_PORTB_BASE, GPIO_PIN_3);
}

void check_i2c_bus_status(void)
{
    // configure as inputs to read
    GPIOPinTypeGPIOInput(GPIO_PORTB_BASE, GPIO_PIN_2 | GPIO_PIN_3);
    delay_us(10);
    uint32_t pins = GPIOPinRead(GPIO_PORTB_BASE, GPIO_PIN_2 | GPIO_PIN_3);

    if((pins & GPIO_PIN_2) == 0 || (pins & GPIO_PIN_3) == 0) {
        recover_i2c_bus();
    } else {
        // restore I2C config
        GPIOPinConfigure(GPIO_PB2_I2C0SCL);
        GPIOPinConfigure(GPIO_PB3_I2C0SDA);
        GPIOPinTypeI2CSCL(GPIO_PORTB_BASE, GPIO_PIN_2);
        GPIOPinTypeI2C(GPIO_PORTB_BASE, GPIO_PIN_3);
    }
}

// ---------- basic I2C write/read ----------
bool mpu9250_writeByte(uint8_t registerAddr, uint8_t data)
{
    uint32_t timeout_counter;
    uint8_t retry_count;

    for(retry_count = 0; retry_count < I2C_TIMEOUT_ATTEMPTS; retry_count++) {
        check_i2c_bus_status();
        I2CMasterInitExpClk(I2C0_BASE, SysCtlClockGet(), false);
        I2CMasterSlaveAddrSet(I2C0_BASE, devAddr, false);

        I2CMasterDataPut(I2C0_BASE, registerAddr);
        I2CMasterControl(I2C0_BASE, I2C_MASTER_CMD_BURST_SEND_START);

        timeout_counter = 0;
        while(I2CMasterBusy(I2C0_BASE) && (timeout_counter < I2C_BUSY_TIMEOUT)) timeout_counter++;

        if(timeout_counter >= I2C_BUSY_TIMEOUT || I2CMasterErr(I2C0_BASE) != I2C_MASTER_ERR_NONE) {
            SysCtlPeripheralReset(SYSCTL_PERIPH_I2C0);
            delay_ms(1);
            continue;
        }

        I2CMasterDataPut(I2C0_BASE, data);
        I2CMasterControl(I2C0_BASE, I2C_MASTER_CMD_BURST_SEND_FINISH);

        timeout_counter = 0;
        while(I2CMasterBusy(I2C0_BASE) && (timeout_counter < I2C_BUSY_TIMEOUT)) timeout_counter++;

        if(I2CMasterErr(I2C0_BASE) == I2C_MASTER_ERR_NONE) return true;

        SysCtlPeripheralReset(SYSCTL_PERIPH_I2C0);
        delay_ms(5);
    }
    return false;
}

bool mpu9250_readBytes(uint8_t registerAddr, uint8_t bytes, uint8_t* data)
{
    uint32_t timeout_counter;
    uint8_t retry_count;

    for(retry_count = 0; retry_count < I2C_TIMEOUT_ATTEMPTS; retry_count++) {
        check_i2c_bus_status();
        I2CMasterInitExpClk(I2C0_BASE, SysCtlClockGet(), false);

        I2CMasterSlaveAddrSet(I2C0_BASE, devAddr, false);
        I2CMasterDataPut(I2C0_BASE, registerAddr);
        I2CMasterControl(I2C0_BASE, I2C_MASTER_CMD_BURST_SEND_START);

        timeout_counter = 0;
        while(I2CMasterBusy(I2C0_BASE) && (timeout_counter < I2C_BUSY_TIMEOUT)) timeout_counter++;

        if(timeout_counter >= I2C_BUSY_TIMEOUT) { SysCtlPeripheralReset(SYSCTL_PERIPH_I2C0); delay_ms(1); continue; }
        if(I2CMasterErr(I2C0_BASE) != I2C_MASTER_ERR_NONE) { SysCtlPeripheralReset(SYSCTL_PERIPH_I2C0); delay_ms(1); continue; }

        I2CMasterSlaveAddrSet(I2C0_BASE, devAddr, true);
        I2CMasterControl(I2C0_BASE, I2C_MASTER_CMD_BURST_RECEIVE_START);

        bool read_success = true;
        uint8_t bytes_remaining = bytes;
        uint8_t data_index = 0;

        while(bytes_remaining > 0 && read_success) {
            timeout_counter = 0;
            while(I2CMasterBusy(I2C0_BASE) && (timeout_counter < I2C_BUSY_TIMEOUT)) timeout_counter++;

            if(timeout_counter >= I2C_BUSY_TIMEOUT) { read_success = false; break; }

            if(I2CMasterErr(I2C0_BASE) == I2C_MASTER_ERR_NONE) {
                data[data_index++] = I2CMasterDataGet(I2C0_BASE);
            } else {
                read_success = false;
                break;
            }

            bytes_remaining--;
            if(bytes_remaining > 0) {
                if(bytes_remaining == 1) I2CMasterControl(I2C0_BASE, I2C_MASTER_CMD_BURST_RECEIVE_FINISH);
                else I2CMasterControl(I2C0_BASE, I2C_MASTER_CMD_BURST_RECEIVE_CONT);
            }
        }

        if(read_success) return true;

        SysCtlPeripheralReset(SYSCTL_PERIPH_I2C0);
        delay_ms(5);
    }

    return false;
}

// ---------- MPU init ----------
void mpu9250_init()
{
    // ensure peripherals enabled
    SysCtlPeripheralEnable(SYSCTL_PERIPH_GPIOB);
    while(!SysCtlPeripheralReady(SYSCTL_PERIPH_GPIOB));

    SysCtlPeripheralEnable(SYSCTL_PERIPH_I2C0);
    while(!SysCtlPeripheralReady(SYSCTL_PERIPH_I2C0));

    // reset I2C
    SysCtlPeripheralReset(SYSCTL_PERIPH_I2C0);
    delay_ms(10);

    // check bus and recover if necessary
    check_i2c_bus_status();

    // configure I2C pins PB2 (SCL), PB3 (SDA)
    GPIOPinConfigure(GPIO_PB2_I2C0SCL);
    GPIOPinConfigure(GPIO_PB3_I2C0SDA);
    GPIOPinTypeI2CSCL(GPIO_PORTB_BASE, GPIO_PIN_2);
    GPIOPinTypeI2C(GPIO_PORTB_BASE, GPIO_PIN_3);

    delay_ms(100);

    // reset MPU
    mpu9250_writeByte(0x6B, 0x80);
    delay_ms(100);

    // Wake and set clock source
    mpu9250_writeByte(0x6B, 0x01);
    delay_ms(10);

    // Gyro ±500 dps (0x08), Accel ±2g (0x00)
    mpu9250_writeByte(0x1B, 0x08);
    mpu9250_writeByte(0x1C, 0x00);

    // DLPF ~41Hz
    mpu9250_writeByte(0x1A, 0x03);

    // disable I2C master
    mpu9250_writeByte(0x24, 0x00);
    delay_ms(10);
}

// ---------- bias calibration (accel + gyro) ----------
#define NUM_CALIBRATION_SAMPLES 500
static float accel_bias[3] = {0.0f, 0.0f, 0.0f};
static bool accel_bias_calibrated = false;

bool mpu9250_calculate_bias(void)
{
    float sum[3] = {0.0f,0.0f,0.0f};
    uint8_t buf[6];
    uint32_t valid = 0;

    uint16_t i;
    for(i=0;i<NUM_CALIBRATION_SAMPLES;i++){
        if(mpu9250_readBytes(ACCEL_ADDR, 6, buf)){
            int16_t raw0 = (int16_t)((buf[0]<<8) | buf[1]);
            int16_t raw1 = (int16_t)((buf[2]<<8) | buf[3]);
            int16_t raw2 = (int16_t)((buf[4]<<8) | buf[5]);
            float ax = raw0 / 16384.0f;
            float ay = raw1 / 16384.0f;
            float az = raw2 / 16384.0f;
            sum[0]+=ax; sum[1]+=ay; sum[2]+=az;
            valid++;
        }
        delay_ms(2);
    }

    if(valid>0){
        accel_bias[0]=sum[0]/valid;
        accel_bias[1]=sum[1]/valid;
        accel_bias[2]=sum[2]/valid - 1.0f; // subtract gravity
        accel_bias_calibrated = true;
        return true;
    }
    return false;
}

void mpu9250_apply_bias_correction(float* accelXYZ)
{
    if(accel_bias_calibrated){
        accelXYZ[0] -= accel_bias[0];
        accelXYZ[1] -= accel_bias[1];
        accelXYZ[2] -= accel_bias[2];
    }
}

// ---------- Accel read with median + LPF ----------
void mpu9250_readAcceleration(uint8_t* accelArray, float* accelXYZ)
{
    uint8_t accel_reg[6];
    int16_t accel_raw[3];

    if(!mpu9250_readBytes(ACCEL_ADDR, 6, accel_reg)){
        accelXYZ[0]=accelXYZ[1]=accelXYZ[2]=0.0f;
        return;
    }

    accel_raw[0] = (int16_t)((accel_reg[0]<<8) | accel_reg[1]);
    accel_raw[1] = (int16_t)((accel_reg[2]<<8) | accel_reg[3]);
    accel_raw[2] = (int16_t)((accel_reg[4]<<8) | accel_reg[5]);

    float ax = accel_raw[0] / 16384.0f;
    float ay = accel_raw[1] / 16384.0f;
    float az = accel_raw[2] / 16384.0f;

    // ring buffers for median
    static float ax_buf[ACCEL_MEDIAN_SAMPLES] = {0}, ay_buf[ACCEL_MEDIAN_SAMPLES] = {0}, az_buf[ACCEL_MEDIAN_SAMPLES] = {0};
    static uint8_t buf_index = 0;

    ax_buf[buf_index] = ax;
    ay_buf[buf_index] = ay;
    az_buf[buf_index] = az;
    buf_index = (buf_index + 1) % ACCEL_MEDIAN_SAMPLES;

    float ax_med = median3(ax_buf[0], ax_buf[1], ax_buf[2]);
    float ay_med = median3(ay_buf[0], ay_buf[1], ay_buf[2]);
    float az_med = median3(az_buf[0], az_buf[1], az_buf[2]);

    static float ax_lpf=0.0f, ay_lpf=0.0f, az_lpf=0.0f;
    const float dt_default = 0.01f; // 10ms default
    ax_lpf = lpf_update(ax_lpf, ax_med, dt_default, ACCEL_LPF_TAU);
    ay_lpf = lpf_update(ay_lpf, ay_med, dt_default, ACCEL_LPF_TAU);
    az_lpf = lpf_update(az_lpf, az_med, dt_default, ACCEL_LPF_TAU);

    accelXYZ[0]=ax_lpf;
    accelXYZ[1]=ay_lpf;
    accelXYZ[2]=az_lpf;

    mpu9250_apply_bias_correction(accelXYZ);
}

// ---------- Gyro raw & bias corrected ----------
static float gyro_bias[3] = {0};
static bool gyro_bias_calibrated = false;

bool mpu9250_read_gyro_raw(int16_t* gyroXYZ)
{
    uint8_t buf[6];
    if(mpu9250_readBytes(GYRO_ADDR,6,buf)){
        gyroXYZ[0] = (int16_t)((buf[0]<<8)|buf[1]);
        gyroXYZ[1] = (int16_t)((buf[2]<<8)|buf[3]);
        gyroXYZ[2] = (int16_t)((buf[4]<<8)|buf[5]);
        return true;
    }
    gyroXYZ[0]=gyroXYZ[1]=gyroXYZ[2]=0;
    return false;
}

bool mpu9250_read_gyro_dps(float* gyroXYZ)
{
    int16_t raw[3];
    if(!mpu9250_read_gyro_raw(raw)){
        gyroXYZ[0]=gyroXYZ[1]=gyroXYZ[2]=0.0f;
        return false;
    }
    // ±500 dps => sensitivity ~65.5 LSB/dps
    const float scale = 1.0f / 65.5f;
    gyroXYZ[0] = raw[0] * scale;
    gyroXYZ[1] = raw[1] * scale;
    gyroXYZ[2] = raw[2] * scale;
    return true;
}

bool mpu9250_calibrate_gyro_bias(void)
{
    float sum[3]={0};
    float tmp[3];
    uint32_t valid=0;
    uint16_t i;
    for(i=0;i<500;i++){
        if(mpu9250_read_gyro_dps(tmp)){
            sum[0]+=tmp[0]; sum[1]+=tmp[1]; sum[2]+=tmp[2];
            valid++;
        }
        delay_ms(2);
    }
    if(valid>0){
        gyro_bias[0]=sum[0]/valid;
        gyro_bias[1]=sum[1]/valid;
        gyro_bias[2]=sum[2]/valid;
        gyro_bias_calibrated = true;
        return true;
    }
    return false;
}

bool mpu9250_read_gyro_dps_corrected(float* gyroXYZ)
{
    if(!mpu9250_read_gyro_dps(gyroXYZ)) return false;
    if(gyro_bias_calibrated){
        gyroXYZ[0] -= gyro_bias[0];
        gyroXYZ[1] -= gyro_bias[1];
        gyroXYZ[2] -= gyro_bias[2];
    }
    return true;
}

void mpu9250_get_gyro(float* gyroXYZ)
{
    mpu9250_read_gyro_dps_corrected(gyroXYZ);
}

// ---------- robust Kalman filter (angle in degrees) ----------
float mpu9250_calculate_pitch_degrees_robust(float accelX, float accelY, float accelZ)
{
    // note: depending on your IMU orientation, you might need to swap axes
    // I've used pitch = atan2(-Y, sqrt(X^2 + Z^2)) (same as your prior code)
    return atan2f(-accelY, sqrtf(accelX*accelX + accelZ*accelZ)) * (180.0f / M_PI);
}

void mpu9250_kalmanFilter(float* pitchFiltered, float* gyroXYZ, float* accelXYZ, float dt)
{
    static float pitchAngle = 0.0f;
    static float pitchBias = 0.0f;
    static float P[2][2] = {{0,0},{0,0}};
    static float accel_angle_lpf = 0.0f;
    static int initialized = 0;

    if(!initialized){
        pitchAngle = mpu9250_calculate_pitch_degrees_robust(accelXYZ[0], accelXYZ[1], accelXYZ[2]);
        accel_angle_lpf = pitchAngle;
        initialized = 1;
    }

    // gyro rate -> pitch rate (dps)
    float gyro_rate_dps = -gyroXYZ[0]; // preserve previous sign convention; test and invert if necessary

    // predict
    float pitchRate = gyro_rate_dps - pitchBias;
    pitchAngle += pitchRate * dt;

    // covariance prediction
    P[0][0] += dt * (dt * P[1][1] - P[0][1] - P[1][0] + KAL_Q_ANGLE);
    P[0][1] -= dt * P[1][1];
    P[1][0] -= dt * P[1][1];
    P[1][1] += KAL_Q_BIAS * dt;

    // measurement
    float pitchAccel = mpu9250_calculate_pitch_degrees_robust(accelXYZ[0], accelXYZ[1], accelXYZ[2]);
    const float accel_angle_tau = 0.03f;
    accel_angle_lpf = lpf_update(accel_angle_lpf, pitchAccel, dt, accel_angle_tau);

    // magnitude check
    float mag = sqrtf(accelXYZ[0]*accelXYZ[0] + accelXYZ[1]*accelXYZ[1] + accelXYZ[2]*accelXYZ[2]);
    float mag_err = fabsf(mag - 1.0f);
    float R_measure_local = KAL_R_MEAS;
    if(mag_err > ACCEL_MAG_THRESHOLD) R_measure_local *= 10.0f; // downweight accel

    // Kalman gain
    float S = P[0][0] + R_measure_local;
    float K0 = P[0][0] / S;
    float K1 = P[1][0] / S;

    float y = accel_angle_lpf - pitchAngle;

    // update
    pitchAngle += K0 * y;
    pitchBias += K1 * y;

    float P00_temp = P[0][0];
    float P01_temp = P[0][1];

    P[0][0] -= K0 * P00_temp;
    P[0][1] -= K0 * P01_temp;
    P[1][0] -= K1 * P00_temp;
    P[1][1] -= K1 * P01_temp;

    *pitchFiltered = pitchAngle;
}

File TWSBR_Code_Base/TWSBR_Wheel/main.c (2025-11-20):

#include <stdbool.h>
#include <stdint.h>
#include <stdlib.h>
#include "inc/hw_memmap.h"
#include "inc/hw_types.h"
#include "inc/hw_gpio.h"
#include "driverlib/gpio.h"
#include "driverlib/sysctl.h"
#include "driverlib/pin_map.h"
#include "driverlib/pwm.h"
#include "driverlib/qei.h"

#include "TWSBR_Wheel.h"

volatile uint32_t ui32Load;
volatile uint32_t ui32PWMClock;
volatile uint32_t ui32SystemClock;
volatile uint32_t ui8Adjust1, ui8Adjust2, ui8Adjust3, ui8Adjust4;

void wheels_init()
{
    SysCtlPeripheralEnable(SYSCTL_PERIPH_GPIOB); // PORTB is used to generate PWM signals
    while(!SysCtlPeripheralReady(SYSCTL_PERIPH_GPIOB));
    SysCtlPeripheralEnable(SYSCTL_PERIPH_GPIOE); // Used to generate ENA signal
    while(!SysCtlPeripheralReady(SYSCTL_PERIPH_GPIOE));
    SysCtlPeripheralEnable(SYSCTL_PERIPH_GPIOD); // Used to read Encoder1 at PD6 and PD7
    while(!SysCtlPeripheralReady(SYSCTL_PERIPH_GPIOD));
    SysCtlPeripheralEnable(SYSCTL_PERIPH_GPIOF); // Used to generate ENB signal at PF0
    while(!SysCtlPeripheralReady(SYSCTL_PERIPH_GPIOF));
    SysCtlPeripheralEnable(SYSCTL_PERIPH_GPIOC); // Used to read Encoder2 at PC5 and PC6
    while(!SysCtlPeripheralReady(SYSCTL_PERIPH_GPIOC));
    SysCtlPeripheralEnable(SYSCTL_PERIPH_QEI0); // Used to read motor2 Encoder
    while(!SysCtlPeripheralReady(SYSCTL_PERIPH_QEI0));
    SysCtlPeripheralEnable(SYSCTL_PERIPH_QEI1);
    while(!SysCtlPeripheralReady(SYSCTL_PERIPH_QEI1));
    SysCtlPWMClockSet(SYSCTL_PWMDIV_4);
    ui32PWMClock = SysCtlPWMClockGet();
    ui32Load = (ui32PWMClock / PWM_FREQUENCY) - 1;

    GPIOPinTypeGPIOOutput(GPIO_PORTE_BASE, GPIO_PIN_4); // Used to set PE4 as EnableA
    HWREG(GPIO_PORTF_BASE + GPIO_O_LOCK) = GPIO_LOCK_KEY;
    HWREG(GPIO_PORTF_BASE + GPIO_O_CR) |= GPIO_PIN_0;
    HWREG(GPIO_PORTF_BASE + GPIO_O_LOCK) = 0;
    GPIOPinTypeGPIOOutput(GPIO_PORTF_BASE, GPIO_PIN_0); // Used to set PF0 as EnableB

    // PB4 and PB5 as PWM outputs for Motor1
    GPIOPinTypePWM(GPIO_PORTB_BASE, GPIO_PIN_4);
    GPIOPinConfigure(GPIO_PB4_M0PWM2);
    GPIOPinTypePWM(GPIO_PORTB_BASE, GPIO_PIN_5);
    GPIOPinConfigure(GPIO_PB5_M0PWM3);

    GPIOPinTypeQEI(GPIO_PORTC_BASE, GPIO_PIN_5 | GPIO_PIN_6);
    GPIOPinConfigure(GPIO_PC5_PHA1);
    GPIOPinConfigure(GPIO_PC6_PHB1);
    QEIConfigure(QEI1_BASE, QEI_CONFIG_CAPTURE_A_B | QEI_CONFIG_NO_RESET | QEI_CONFIG_NO_SWAP, 7000);
    QEIFilterEnable(QEI1_BASE);
    QEIFilterConfigure(QEI1_BASE, QEI_FILTCNT_3);
    QEIPositionSet(QEI1_BASE, 0);
    QEIVelocityEnable(QEI1_BASE);
    QEIEnable(QEI1_BASE);

    // PB6 and PB7 as PWM outputs for Motor2
    GPIOPinTypePWM(GPIO_PORTB_BASE, GPIO_PIN_6);
    GPIOPinConfigure(GPIO_PB6_M0PWM0);
    GPIOPinTypePWM(GPIO_PORTB_BASE, GPIO_PIN_7);
    GPIOPinConfigure(GPIO_PB7_M0PWM1);

    HWREG(GPIO_PORTD_BASE + GPIO_O_LOCK) = GPIO_LOCK_KEY;
    HWREG(GPIO_PORTD_BASE + GPIO_O_CR) |= GPIO_PIN_6 | GPIO_PIN_7;
    HWREG(GPIO_PORTD_BASE + GPIO_O_LOCK) = 0;

    GPIOPinTypeQEI(GPIO_PORTD_BASE, GPIO_PIN_6 | GPIO_PIN_7);
    GPIOPinConfigure(GPIO_PD6_PHA0);
    GPIOPinConfigure(GPIO_PD7_PHB0);
    QEIConfigure(QEI0_BASE, QEI_CONFIG_CAPTURE_A_B | QEI_CONFIG_NO_RESET | QEI_CONFIG_SWAP, 7000);
    QEIFilterEnable(QEI0_BASE);
    QEIFilterConfigure(QEI0_BASE, QEI_FILTCNT_3);
    QEIPositionSet(QEI0_BASE, 0);
    QEIVelocityEnable(QEI0_BASE);
    QEIEnable(QEI0_BASE);

    // PB4, PB5, PB6, PB7 get their PWM from Module0
    SysCtlPeripheralEnable(SYSCTL_PERIPH_PWM0);
    while(!SysCtlPeripheralReady(SYSCTL_PERIPH_PWM0));

    // (PB6 and PB7) get PWM from generator 0
    PWMGenConfigure(PWM0_BASE, PWM_GEN_0, PWM_GEN_MODE_DOWN);
    PWMGenPeriodSet(PWM0_BASE, PWM_GEN_0, ui32Load);

    // (PB4 and PB5) get PWM from generator 1
    PWMGenConfigure(PWM0_BASE, PWM_GEN_1, PWM_GEN_MODE_DOWN);
    PWMGenPeriodSet(PWM0_BASE, PWM_GEN_1, ui32Load);

    // Set initial duty cycles (motors stopped)
    PWMPulseWidthSet(PWM0_BASE, PWM_OUT_2, ui32Load/2); // PB4 - Motor 1 IN1
    PWMPulseWidthSet(PWM0_BASE, PWM_OUT_3, ui32Load/2); // PB5 - Motor 1 IN2
    PWMPulseWidthSet(PWM0_BASE, PWM_OUT_0, ui32Load/2); // PB6 - Motor 2 IN1
    PWMPulseWidthSet(PWM0_BASE, PWM_OUT_1, ui32Load/2); // PB7 - Motor 2 IN2

    // Set Output State of PWM_outputs to true
    PWMOutputState(PWM0_BASE, PWM_OUT_0_BIT, true);
    PWMOutputState(PWM0_BASE, PWM_OUT_1_BIT, true);
    PWMOutputState(PWM0_BASE, PWM_OUT_2_BIT, true);
    PWMOutputState(PWM0_BASE, PWM_OUT_3_BIT, true);

    // Enable PWM Generator0 and Generator1
    PWMGenEnable(PWM0_BASE, PWM_GEN_0);
    PWMGenEnable(PWM0_BASE, PWM_GEN_1);

    // Enable Pins HIGH to drive the motors
    GPIOPinWrite(GPIO_PORTE_BASE, GPIO_PIN_4, GPIO_PIN_4); // Set EnableA HIGH to run motor1
    GPIOPinWrite(GPIO_PORTF_BASE, GPIO_PIN_0, GPIO_PIN_0); // Set EnableB HIGH to run motor2
}

void wheels_getPosition(uint32_t* posn_array)
{
    posn_array[0] = QEIPositionGet(QEI0_BASE);
    posn_array[1] = QEIPositionGet(QEI1_BASE);
}

void wheel_setSpeed(float control_input, int8_t wheel_id)
{
    float max_input = (float)(ui32Load/2);
    if(control_input >= max_input) { control_input = max_input-1; }
    else if(control_input <= -max_input) { control_input = -max_input+1; }

    int32_t adjusted_input = (int32_t)control_input;
    uint32_t halfLoad = ui32Load / 2;

    if(wheel_id == 1)
    {
        // Motor 1: PB4 (M0PWM2) and PB5 (M0PWM3)
        ui8Adjust1 = halfLoad + adjusted_input;  // PB4
        ui8Adjust2 = halfLoad - adjusted_input;  // PB5
        PWMPulseWidthSet(PWM0_BASE, PWM_OUT_2, ui8Adjust1); // CORRECT: PB4
        PWMPulseWidthSet(PWM0_BASE, PWM_OUT_3, ui8Adjust2); // CORRECT: PB5
    }
    else if(wheel_id == 2)  // Use 2 instead of -1
    {
        // Motor 2: PB6 (M0PWM0) and PB7 (M0PWM1)
        ui8Adjust3 = halfLoad - adjusted_input;  // PB6
        ui8Adjust4 = halfLoad + adjusted_input;  // PB7
        PWMPulseWidthSet(PWM0_BASE, PWM_OUT_0, ui8Adjust3); // CORRECT: PB6
        PWMPulseWidthSet(PWM0_BASE, PWM_OUT_1, ui8Adjust4); // CORRECT: PB7
    }
    else
    {
        // Both motors (wheel_id = 0)
        ui8Adjust1 = halfLoad + adjusted_input;
        ui8Adjust2 = halfLoad - adjusted_input;
        ui8Adjust3 = halfLoad - adjusted_input;
        ui8Adjust4 = halfLoad + adjusted_input;

        // Motor 1
        PWMPulseWidthSet(PWM0_BASE, PWM_OUT_2, ui8Adjust1); // PB4
        PWMPulseWidthSet(PWM0_BASE, PWM_OUT_3, ui8Adjust2); // PB5

        // Motor 2
        PWMPulseWidthSet(PWM0_BASE, PWM_OUT_0, ui8Adjust3); // PB6
        PWMPulseWidthSet(PWM0_BASE, PWM_OUT_1, ui8Adjust4); // PB7
    }
}

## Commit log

2025-11-01 Board pinout
2025-11-01 Connection Summary
    [TivaC_Board_Connections.csv]
2025-11-02 TWSBR_Wheel Library
    Added motor actuation methods
2025-11-06 improved the i2c communication error
    incorporated error detection and restart logic
    [main.c]
2025-11-06 Control_logic_incorporated anlong with sensor integration
2025-11-06 PID Controller implemented
2025-11-18 PID Tuner based on Pico
2025-11-18 Integrated ESP communication
    PID implementation with ESP left
2025-11-28 Add ESP01 connections to TivaC Board CSV
    [TivaC_Board_Connections.csv]
2025-11-28 Add ESP01 pin connections to README
2025-11-28 Update TivaC board connections for ESP01 and MPU9250 and RLS08
    [TivaC_Board_Connections.csv]
2025-11-28 Added Mechanical Subsystem
    [Level0.DXF, Level1.DXF]
